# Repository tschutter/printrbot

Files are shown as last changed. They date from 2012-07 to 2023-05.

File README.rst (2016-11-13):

printrbot
=========

All things needed to drive my Printrbot Plus V1.

Usage
-----
::

    sudo apt-get install python-serial python-wxgtk2.8 python-pyglet openscad
    sudo -H pip install --upgrade numpy pyglet # for Printrun
    git clone --recursive git@github.com:tschutter/printrbot.git
    cd printrbot
    git submodule init
    git submodule update
    wget -P /tmp http://dl.slic3r.org/linux/slic3r-linux-x86-1-0-1-stable.tar.gz
    tar xzf /tmp/slic3r-linux-*.tar.gz

Tools
-----

* `Slic3r`_ takes a 3D model and converts (slices) it into printer
  instructions (G-code) for a 3D printer.  It's main competitors are
  `Skeinforge`_, `Cura`_, and `Makerware`_.  A comparison of these
  tools can be found at `Skeinforge(RepG) vs Cura vs Makerware vs
  Slic3r et al`_.

* `OpenSCAD`_ "The Programmers Solid 3D CAD Modeller" is used for
  creating solid 3D CAD models.  OpenSCAD is not an interactive
  modeller. Instead it is a compiler that reads in a script file that
  describes the object and renders the 3D model from this script file.

* `SOLVESPACE`_ is a parametric 3d CAD program.

Calibration
-----------

The Z-axis end stop should be adjusted so that you can slip two
thicknesses of index card between the print head and the print bed.

When adjusting the Z-axis end stop, you must press the "Z-home" button
instead of just using the Z-axis move buttons.  When using the move
buttons, the hardware will not lower print head below what it thinks
the Z = 0 position, which is set the last time you powered up the
printer or pressed "Z-Home".

Modifications
-------------

Nobody runs a stock Printrbot, and mine is no exception.

* Stiffened the X-axis with a piece of 1/2" aluminum U-channel 14" long.

* Added a 50mm cooling fan using a printed `Printbot LC 50mm Fan
  Mount`_ to prevent the extruder from melting previously printed
  layers.  Slic3r must be called with the --cooling option to enable
  `fan control`_.

* Covered the heated printer bed with a 9" by 9" piece of glass to
  prevent bed warping.

* Placed a 9" by 9" by 3/16" cork tile under the heated printer bed
  for thermal insulation.

* Replaced the extruder herringbone gears with `Spur Gears`_.
  Herringbone gears are intended for high-speed applications.  Their
  use is not appropriate for the extruder and min original gears were
  slightly warped.

Slic3r Config
-------------

With each new version of Slic3r, the configuration file changes.  It
is easiest to export a new .ini file from Slic3r and modify it as
follows.

* ``filament_diameter = 2.95``

    Measured with a caliper at various points along the filament.

* ``first_layer_bed_temperature = 80``

    Current suggestion by the web for ABS.

* ``bed_temperature = 75``

    Current suggestion by the web for ABS.

* ``first_layer_temperature = 230``

    Current suggestion by the web for ABS.

* ``temperature = 230``

    Current suggestion by the web for ABS.

* ``first_layer_height = 0.25``

    Sounds about right.

* ``layer_height = 0.2``

    Sounds about right.

* ``start_gcode = DEFAULT + \nM92 X62.7\nM92 Y62.8\nM92 Z2387.0719\nM92 E536``

    Adjust axis_steps_per_unit for each axis and extruder.  Probably
    set in 2012 based upon the print of a 40mm cube.

* ``min_skirt_length = 4``

    Impose a minimum skirt length to ensure that the extruder is
    primed.  This compensates for the filament that oozes from the
    extruder when we are waiting for everything to come up to the
    proper temperature.  Note that the value is supposed to be in mm,
    but it is most certainly not.  The correct value here is 250 mm.

* ``max_fan_speed = 55``

    If the fan runs at 100% of the rated speed, it cools the part (or
    the print bed) so much that it tends to pop off of the print bed
    after a dozen or so layers.  Using a fan duct may improve this
    problem.  With no fan duct, a max speed of 65% resulted in pop
    off.

Links
-----

* `Printrun (pronterface and pronsole)
  <https://github.com/kliment/Printrun>`__

* `Using slic3r with pronterface
  <http://www.printrbottalk.com/wiki/index.php?title=Using_slic3r_with_pronterface>`__

* `Printrun @ RepRap wiki <http://reprap.org/wiki/Printrun>`__

.. _Slic3r: http://slic3r.org/
.. _fan control: http://manual.slic3r.org/Cooling.html
.. _Skeinforge: http://reprap.org/wiki/Skeinforge/
.. _Cura: http://software.ultimaker.com/
.. _Makerware: https://www.makerbot.com/makerware/
.. _Skeinforge(RepG) vs Cura vs Makerware vs Slic3r et al: https://groups.google.com/forum/#!topic/flashforge/D1VHlkvOLxg
.. _OpenSCAD: http://www.openscad.org/
.. _SOLVESPACE: http://solvespace.com/
.. _Printbot LC 50mm Fan Mount: http://www.thingiverse.com/thing:26775
.. _Spur Gears: http://www.thingiverse.com/thing:26243
.. _G-code: http://reprap.org/wiki/G-code

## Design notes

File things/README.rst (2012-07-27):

Things
======

This directory contains various 3-D things that can be printed.

Other Interesting Things
------------------------

* `Hobby Lathe Produced by 3D Printing
  <http://www.robots-dreams.com/2012/05/hobby-lathe-produced-by-3d-printing-video.html>`__,
  `@ github
  <https://github.com/Intrinsically-Sublime/Printable-Lathe-V2>`__,
  `@ hackaday
  <http://hackaday.com/2012/05/21/3d-printing-a-mini-lathe/>`__

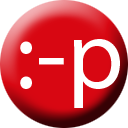
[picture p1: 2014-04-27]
P-face.png

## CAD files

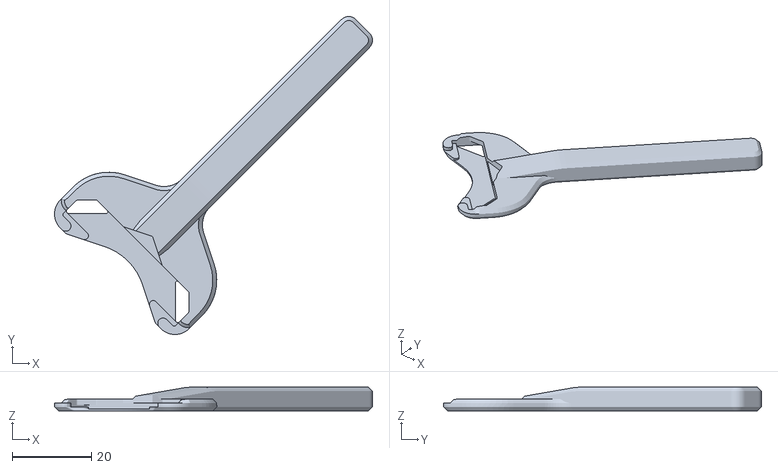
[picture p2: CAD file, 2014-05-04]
things/tiv-034481-razor-handle.stl
80.3 x 80.3 x 6.00

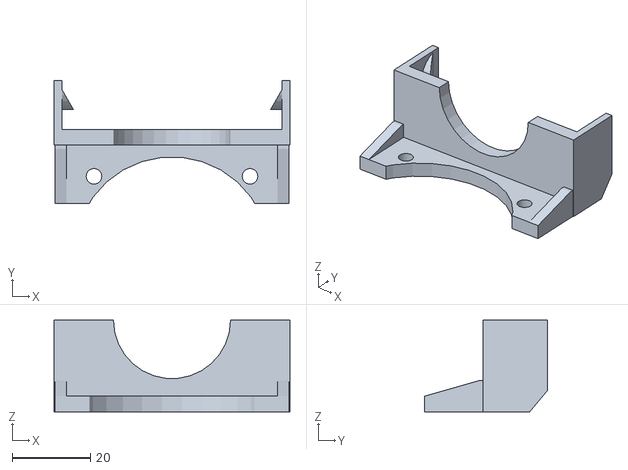
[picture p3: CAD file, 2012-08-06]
things/tiv-026775-PrinterBot_LC_Fan_Mount2.stl
60.5 x 31.6 x 23.5

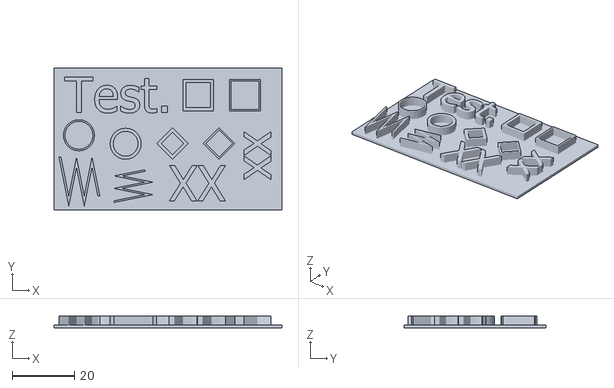
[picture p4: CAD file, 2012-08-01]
things/tiv-023965-test.stl
73.2 x 45.7 x 4.00

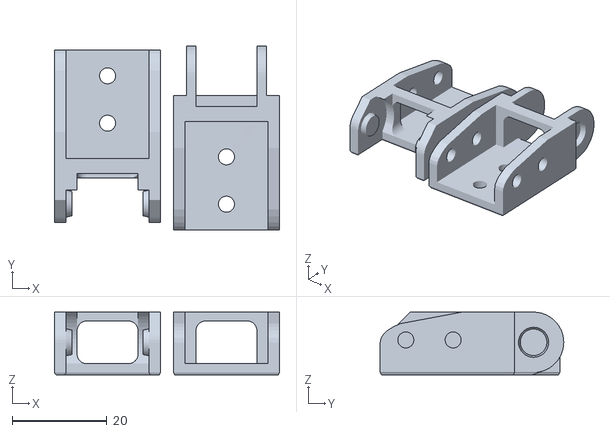
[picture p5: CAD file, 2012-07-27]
things/tiv-011978-CableChainEnds.stl
47.6 x 38.8 x 13.3

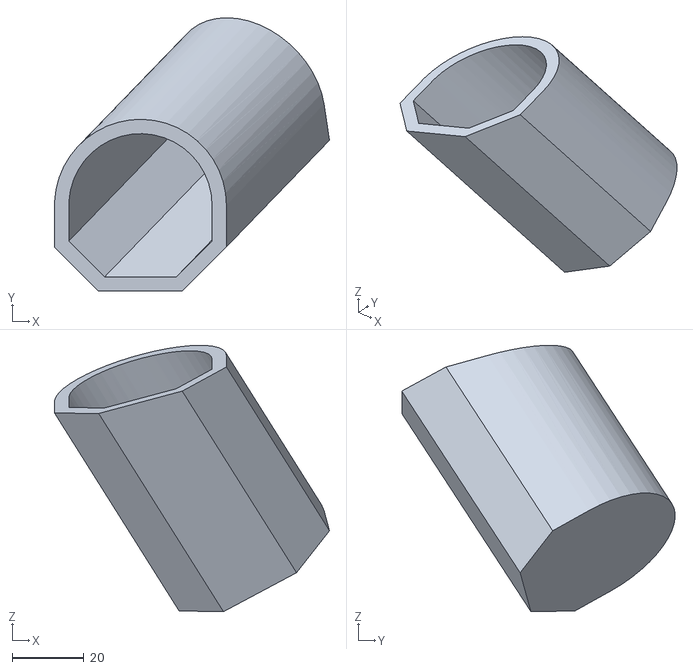
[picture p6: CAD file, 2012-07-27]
things/tiv-001929-mouse_roll_trap_top.stl
76.8 x 76.4 x 74.4

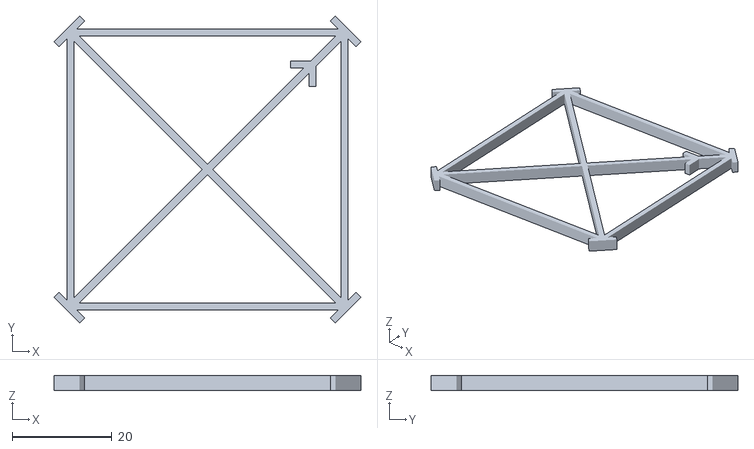
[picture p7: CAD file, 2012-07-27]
things/tiv-012820-SquareCal.stl
61.7 x 61.7 x 3.00

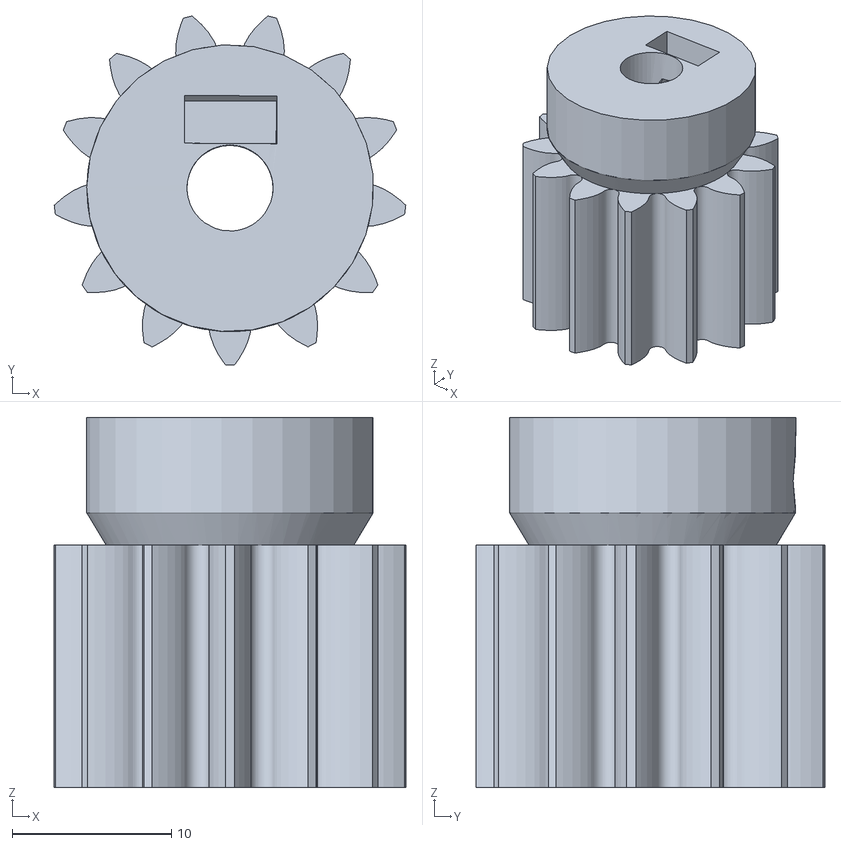
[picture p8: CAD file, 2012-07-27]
things/tiv-026243-S_Gear_Spur_V1.stl
22.1 x 21.9 x 23.2

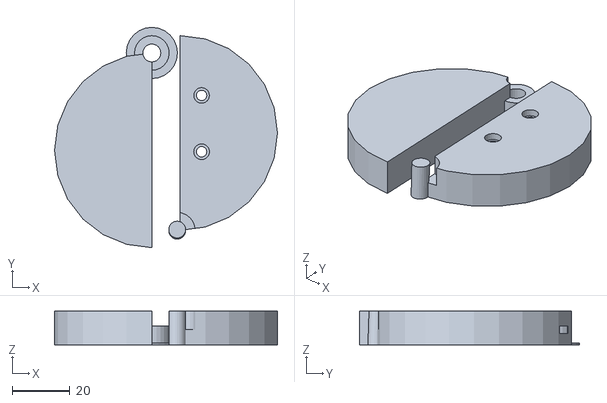
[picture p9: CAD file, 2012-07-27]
things/tiv-021977-Filament_Clipper_delta.stl
77.2 x 76.3 x 11.7

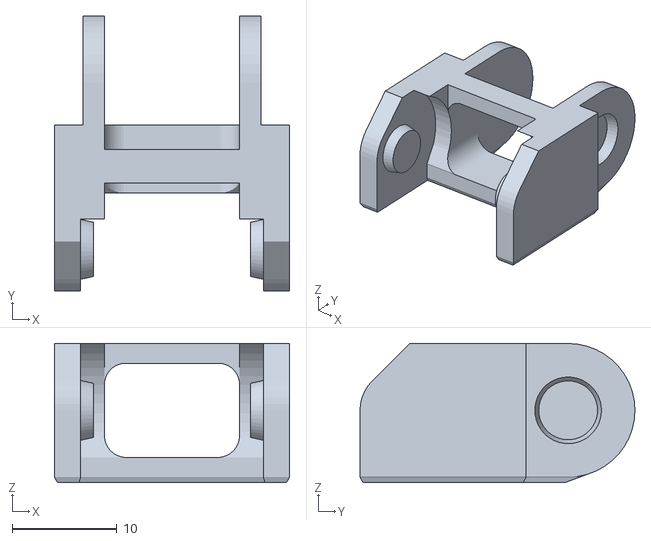
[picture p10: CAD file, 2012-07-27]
things/tiv-011978-CableChain.stl
22.4 x 26.3 x 13.3

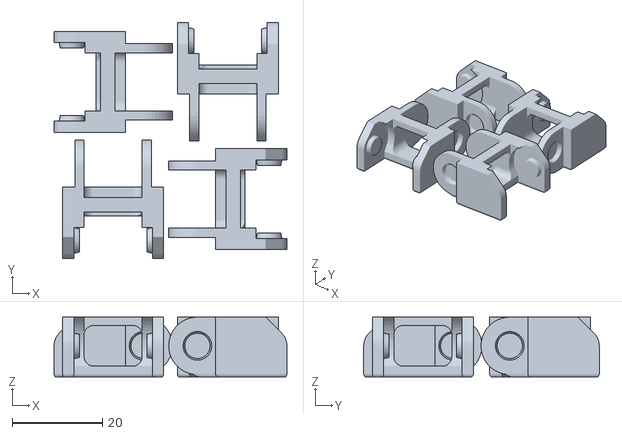
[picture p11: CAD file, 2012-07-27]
things/tiv-011978-CableChainx4.stl
51.7 x 52.3 x 13.3

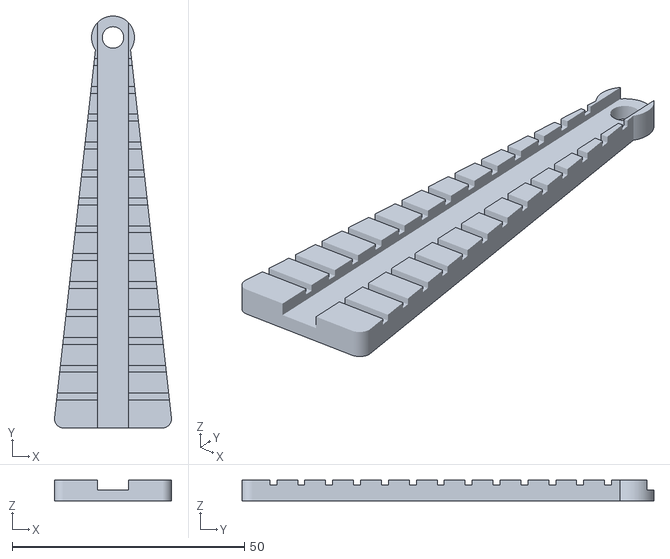
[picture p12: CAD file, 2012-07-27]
things/tiv-026025-narrow-short-imperial.stl
25.2 x 88.6 x 4.50

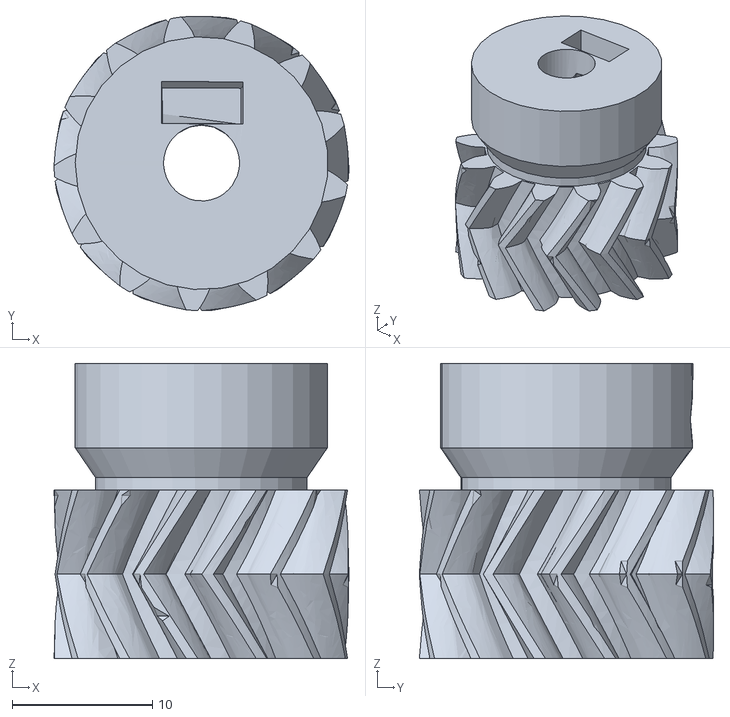
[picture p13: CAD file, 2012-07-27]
things/tiv-016990-ESmgr1.stl
21.0 x 21.0 x 21.0

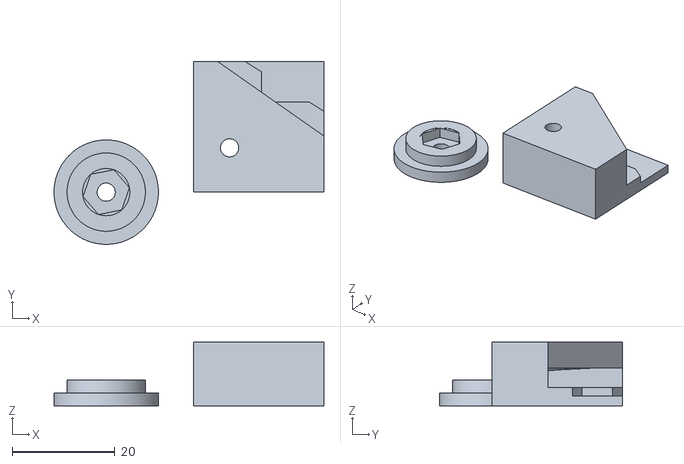
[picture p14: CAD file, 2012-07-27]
things/tiv-027269-GlassClipAdjust_LF_RR.stl
52.5 x 35.5 x 12.4

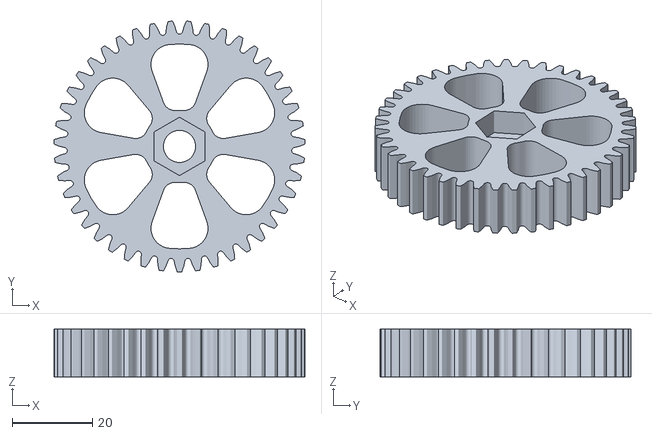
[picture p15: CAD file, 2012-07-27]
things/tiv-026243-L_Gear_Spur_V2.stl
62.5 x 62.5 x 11.9

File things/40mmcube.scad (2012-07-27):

// A 40mm cube for calibration.  Inspired by
// http://www.thingiverse.com/thing:477.

cube(size=[40, 40, 40]);

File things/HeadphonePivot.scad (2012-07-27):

// Attachment pivot between the head strap and the earpiece on a set
// of iHome headphones.

// number of faces on each cylinder
$fn=120;

scale([25.4, 25.4, 25.4]) {
    union() {
        // cylinder base
        difference() {
            cylinder(h=0.125, r=0.1, center=false);
            translate([0, 0, -0.05]) {
                cylinder(h=0.225, r=0.05, center=false);
            }
        }
        // conical top
        intersection() {
            difference() {
                translate([0, 0, 0.125]) {
                    cylinder(h=0.125, r1=0.1, r2=0.225, center=false);
                }
                translate([0, 0, 0.124]) {
                    cylinder(h=0.126, r1=0.079, r2=0.155, center=false);
                }
            }
            // bevel
            cylinder(h=0.3, r=0.2, center=false);
        }
    }
}

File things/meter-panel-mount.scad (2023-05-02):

// Surface-mount box for CGELE DC Multifunction Battery Monitor Meter
// https://www.amazon.com/gp/product/B08Y61CNLK
//
// Inspired by https://www.thingiverse.com/thing:5331402

use <roundedcube.scad>

// Dimensions of hole for meter.
hole_size_x = 87;
hole_size_y = 47;
hole_corner_radius = 3.5;

// Dimensions of body.
body_size_x = 110;
body_size_y = 70;
body_size_z = 30;
body_radius = 2;
body_thickness = 3;

// Dimensions of screw tabs.
tab_size_x = 25;
tab_size_y = 25;
tab_size_z = 6;  // due to a bug in roundedcube, must be >= 3 * body_radius

// Dimension of screw holes.
screw_hole_radius = 2.6;  // #8 or #10 wood screw

// Dimension of wire hole.
wire_hole_radius = 3;

$fs = 0.15;

difference() {
  difference() {
    union() {
      // body
      roundedcube([body_size_x, body_size_y, body_size_z], true, body_radius, "zmax");

      // all tabs
      tab_offset_y = body_size_y / 2 - tab_size_y / 2;
      tab_offset_z = -(body_size_z / 2 - tab_size_z / 2);

      // ymin tabs
      translate([0, -tab_offset_y, tab_offset_z])
        roundedcube([body_size_x + tab_size_x * 2, tab_size_y, tab_size_z], true, body_radius, "zmax");

      // ymax tabs
      translate([0, tab_offset_y, tab_offset_z])
        roundedcube([body_size_x + tab_size_x * 2, tab_size_y, tab_size_z], true, body_radius, "zmax");

      // all tabs
      wing_offset_x_0 = body_size_x / 2 - body_radius;
      wing_offset_x_1 = body_size_x / 2 + tab_size_x - body_radius;
      wing_offset_x_2 = wing_offset_x_0;
      wing_offset_y = body_size_y / 2 - body_radius;
      wing_offset_z_0 = -body_size_z / 2 + tab_size_z - body_radius;
      wing_offset_z_1 = wing_offset_z_0;
      wing_offset_z_2 = body_size_z / 2 - body_radius;

      // xmin, ymin wing
      hull() {
        translate(v = [-wing_offset_x_0, -wing_offset_y, wing_offset_z_0])
          sphere(r = body_radius);
        translate(v = [-wing_offset_x_1, -wing_offset_y, wing_offset_z_1])
          sphere(r = body_radius);
        translate(v = [-wing_offset_x_2, -wing_offset_y, wing_offset_z_2])
          sphere(r = body_radius);
      };

      // xmin, ymax wing
      hull() {
        translate(v = [-wing_offset_x_0, wing_offset_y, wing_offset_z_0])
          sphere(r = body_radius);
        translate(v = [-wing_offset_x_1, wing_offset_y, wing_offset_z_1])
          sphere(r = body_radius);
        translate(v = [-wing_offset_x_2, wing_offset_y, wing_offset_z_2])
          sphere(r = body_radius);
      };

      // xmax, ymin wing
      hull() {
        translate(v = [wing_offset_x_0, -wing_offset_y, wing_offset_z_0])
          sphere(r = body_radius);
        translate(v = [wing_offset_x_1, -wing_offset_y, wing_offset_z_1])
          sphere(r = body_radius);
        translate(v = [wing_offset_x_2, -wing_offset_y, wing_offset_z_2])
          sphere(r = body_radius);
      };

      // xmax, ymax wing
      hull() {
        translate(v = [wing_offset_x_0, wing_offset_y, wing_offset_z_0])
          sphere(r = body_radius);
        translate(v = [wing_offset_x_1, wing_offset_y, wing_offset_z_1])
          sphere(r = body_radius);
        translate(v = [wing_offset_x_2, wing_offset_y, wing_offset_z_2])
          sphere(r = body_radius);
      };
    };
  };

  union() {
    // meter hole
    roundedcube([hole_size_x, hole_size_y, body_size_z + 10], true, hole_corner_radius);

    // screw holes
    hole_offset_x = body_size_x / 2 + tab_size_x / 2;
    hole_offset_y = body_size_y / 2 - tab_size_y / 2;
    hole_offset_z = -body_size_z / 2 + tab_size_z / 2;
    translate([-hole_offset_x, -hole_offset_y, hole_offset_z])
      cylinder(h = tab_size_z + 1, r = screw_hole_radius, center = true);
    translate([-hole_offset_x, hole_offset_y, hole_offset_z])
      cylinder(h = tab_size_z + 1, r = screw_hole_radius, center = true);
    translate([hole_offset_x, -hole_offset_y, hole_offset_z])
      cylinder(h = tab_size_z + 1, r = screw_hole_radius, center = true);
    translate([hole_offset_x, hole_offset_y, hole_offset_z])
      cylinder(h = tab_size_z + 1, r = screw_hole_radius, center = true);

    // wire hole
    translate([body_size_x / 2 - body_thickness / 2, 0, -body_size_z / 2])
      rotate([0, 90, 0])
        cylinder(h = body_thickness + 1, r = wire_hole_radius, center = true);

    // interior space
    interior_size_x = body_size_x - body_thickness * 2;
    interior_size_y = body_size_y - body_thickness * 2;
    translate([0, 0, -body_thickness])
      roundedcube([interior_size_x, interior_size_y, body_size_z], true, body_radius, "zmax");
  };
};

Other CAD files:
things/tiv-027269-GlassClipAdjust_RF_LR.stl
things/tiv-000477-40mmcube.stl
things/tiv-014702-Mr.Jawsv2.stl
things/tiv-001929-mouse_door_rev_a.stl
things/PrinterBotZStop.scad
things/ShelfSupport.scad
things/TrooperDoorLockBushing.scad
things/roundedcube.scad
things/tiv-001929-mouse_roll_trap_base.stl
things/tiv-002154-door-stopper-2.scad
things/tiv-016990-E-Lg-gear.stl
things/tiv-026775-PrinterBot_LC_Fan_Mount2.scad

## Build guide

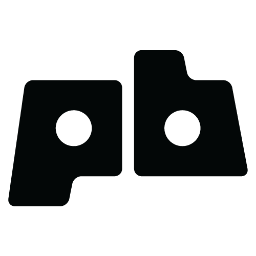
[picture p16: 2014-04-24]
printrbot.png

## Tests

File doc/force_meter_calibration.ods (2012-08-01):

Measured |  |  | Best Fit
Tick | MassG | ForceN | Tick | ForceN
1 | 117 | 1.15 | 0 | 0.73
2 | 156 | 1.53 | 1 | 1.12
3 | 195 | 1.91 | 2 | 1.50
4 | 231 | 2.27 | 3 | 1.89
5 | 268 | 2.63 | 4 | 2.27
6 | 312 | 3.06 | 5 | 2.66
7 | 344 | 3.37 | 6 | 3.05
8 | 377 | 3.70 | 7 | 3.43
9 | 418 | 4.10 | 8 | 3.82
10 | 459 | 4.50 | 9 | 4.20
11 | 522 | 5.12 | 10 | 4.59
12 | 540 | 5.30 | 11 | 4.97
1 | 119 | 1.17 | 12 | 5.36
2 | 155 | 1.52 | 13 | 5.75
3 | 197 | 1.93 | 14 | 6.13
4 | 229 | 2.25 | 15 | 6.52
5 | 274 | 2.69 | 16 | 6.90
6 | 309 | 3.03 | 17 | 7.29
7 | 343 | 3.36 | 18 | 7.68
8 | 392 | 3.85
9 | 430 | 4.22
10 | 464 | 4.55 | slope | intercept
11 | 509 | 4.99 | 0.385899024 | 0.7299527216
12 | 555 | 5.44
1 | 112 | 1.10
2 | 150 | 1.47
3 | 192 | 1.88
4 | 220 | 2.16
5 | 278 | 2.73
6 | 321 | 3.15
7 | 352 | 3.45
8 | 402 | 3.94
9 | 428 | 4.20
10 | 450 | 4.41
11 | 516 | 5.06
12 | 540 | 5.30
13 | 577 | 5.66
14 | 640 | 6.28
15 | 660 | 6.47
16 | 700 | 6.87
17 | 753 | 7.39

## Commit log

2012-06-30 add Printrun and things submodules
2012-06-30 pronsolerc: add commented-out fan button
2012-06-30 Printrbot-Getting-Started-Guide2.pdf: initial checkin
2012-06-30 README.rst: fix printrbot git URL
2012-07-04 abs.ini: calibrated X and Y axis
2012-07-19 pronsolerc: match temperatures to abs.ini
2012-07-27 added content of repository 'things'
    [40mmcube.scad, HeadphonePivot.scad, ShelfSupport.scad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]
2012-08-01 tiv-023965-test.stl: initial checkin
    [tiv-023965-test.stl]
2012-08-01 force_meter_calibration.ods: initial checkin
    [force_meter_calibration.ods]
2012-08-05 abs.ini: calibrated extruder
2012-08-06 tiv-024545-PrintrbotFanMountV3.stl -> tiv-026775-PrinterBot_LC_Fan_Mount2.*
    [tiv-024545-PrintrbotFanMountV3.stl, tiv-026775-PrinterBot_LC_Fan_Mount2.scad, tiv-026775-PrinterBot_LC_Fan_Mount2.stl]
2012-08-15 pronsolerc: bump bed temp to 80
2014-04-24 printrbot.png: initial checkin
2014-04-27 pronsolerc: updated all src/printrbot paths
2014-05-04 tiv-034481-razor-handle.stl: initial checkin
    [tiv-034481-razor-handle.stl]
2014-05-11 README.rst: added OpenSCAD, updated cooling fan info with link
2014-05-11 TrooperDoorLockBushing.scad: initial checkin
    [TrooperDoorLockBushing.scad]
2014-05-12 pronsolerc: bump extruder temp to 230
2014-05-13 enabled fan control
2014-05-17 slic3r-abs.ini: drop fan speed, set min_skirt_length
2014-05-17 README.rst: add Calibration, spur gears, min_skirt_length, max_fan_speed
2014-05-17 README.rst: added fan control info
2014-05-18 pronsolerc: added fan control button
2014-05-18 TrooperDoorLockBushing.scad: fixed dimensions
    [TrooperDoorLockBushing.scad]
2016-11-06 PrinterBotZStop.scad: initial checkin
    [PrinterBotZStop.scad]
2016-11-12 TrooperDoorLockBushing.scad: attempt to compensate for thin wall thickness problem
    [TrooperDoorLockBushing.scad]
2016-11-12 pronsolerc: increase bed temperature from 80 to 110
2016-11-12 PrinterBotZStop.scad: create multiple to explore interior hole adjustments
    [PrinterBotZStop.scad]
2016-11-13 upgraded Printrun to 2016-11-13 version
2023-05-02 meter-panel-mount.scad, roundedcube.scad: initial checkin
    [meter-panel-mount.scad, roundedcube.scad]
2023-05-02 meter-panel-mount.scad: slightly increased size of screw holes
    [meter-panel-mount.scad]
